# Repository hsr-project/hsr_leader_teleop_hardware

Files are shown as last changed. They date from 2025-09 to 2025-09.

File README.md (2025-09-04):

# THSR: Teleoperation Hardware for HSR

This repository publishes 3D data and documentation for a leader-side teleoperation hardware named THSR to be used with the Toyota Human Support Robot (HSR).

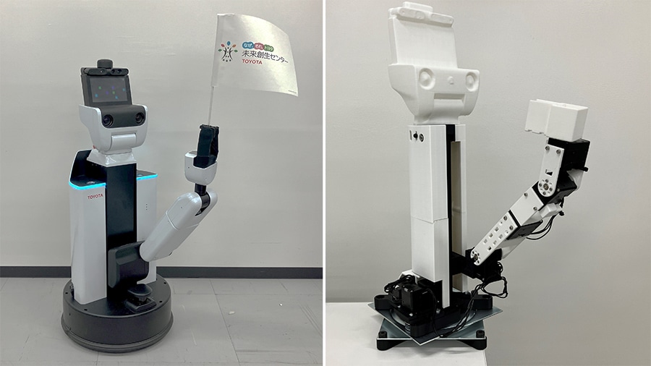
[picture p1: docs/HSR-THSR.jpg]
THSR


## Quick links

- Assembly model: [STEP/THSR-Total-000-A.STEP](STEP/THSR-Total-000-A.STEP)
- Printable parts (examples; see full sets under `STL/THSR-Arm`, `STL/THSR-Lift`, `STL/THSR-Turn`):
  - Arm: [STL/THSR-Arm/THSR-Arm-010.STL](STL/THSR-Arm/THSR-Arm-010.STL), etc.
  - Lift: [STL/THSR-Lift/THSR-Lift-010.STL](STL/THSR-Lift/THSR-Lift-010.STL), etc.
  - Turn: [STL/THSR-Turn/THSR-Turn-010.STL](STL/THSR-Turn/THSR-Turn-010.STL), etc.
- Assembly guide: [docs/THSR-組付手順書.pdf](docs/THSR-組付手順書.pdf)
- Bill of Materials (BOM): [docs/THSR-BOM.csv](docs/THSR-BOM.csv)

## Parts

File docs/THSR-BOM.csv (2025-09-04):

No | Unit | Item Name | Quantity | Remarks
1 | lift-assy | SSEBZ10-235 | 1 | misumi
2 | lift-assy | HTPA14S2M100-K-P3 | 2 | misumi
3 | lift-assy | CLBP3-5-3.5 | 4 | misumi
4 | lift-assy | SB693ZZ | 4 | misumi
5 | lift-assy | HFSB5-2020-264-TPW | 1 | misumi
6 | lift-assy | SSFR3-48-WFC0-J6-W12-V6-TB2 | 1 | misumi
7 | lift-assy | SSFR3-41-TA2-TB2 | 1 | misumi
8 | lift-assy | THSR-Lift-020 | 1 | 3D printed part, Black, PLA
9 | lift-assy | THSR-Lift-050-A | 2 | 3D printed part, Black, PLA
10 | lift-assy | HTBN500S2M-100 | 1 | misumi
11 | lift-assy | THSR-Lift-070 | 1 | 3D printed part, Black, PLA
12 | lift-assy | THSR-Lift-010-A | 1 | 3D printed part, Black, PLA, infill60%
13 | lift-assy | THSR-Lift-090 | 1 | 3D printed part, Black, PLA, infill60%
14 | lift-assy | THSR-Lift-080 | 1 | 3D printed part, Black, PLA
15 | lift-assy | CBE3-15 | 9 | misumi
16 | lift-assy | CBE5-15 | 1 | misumi
17 | lift-assy | CBE3-10 | 14 | misumi
18 | lift-assy | LBNR3 | 14 | misumi
19 | lift-assy | CBE3-6 | 4 | misumi
20 | lift-assy | CSHSM-SUS-M3-5 | 4 | misumi
21 | lift-assy | THSR-Lift-060 | 1 | 3D printed part, Black, PLA, infill60%
22 | lift-assy | SHNTP5-3 | 4 | misumi
23 | lift-assy | CBSH5-16 | 1 | misumi
24 | lift-assy | HTPA24S3M060-A-P6 | 1 | misumi
25 | lift-assy | GEABB0.5-15-8-K-3 | 1 | misumi
26 | pulley-assy | XM430-W210-T | 1 | ROBOTIS
27 | pulley-assy | HILS-turn-shaft-1107 | 1 | Custom part Meviy, MVTUP-APN-3ZM-M1JEH (Meviy part number)
28 | pulley-assy | THSR-Lift-040-A | 1 | 3D printed part, Black, PLA
29 | pulley-assy | SB676ZZ | 2 | misumi
30 | pulley-assy | CBSST2-4 | 4 | misumi
31 | gear-assy | XC-330-T181-T | 1 | ROBOTIS
32 | gear-assy | GEABB0.5-50-2-B-4 | 1 | misumi
33 | gear-assy | HILS-lift-shaft-holder-1113 | 1 | Custom part Meviy, MVTUP-APN-3ZN-NNWBE (Meviy part number)
34 | gear-assy | THSR-Lift-030-A | 1 | 3D printed part, Black, PLA
35 | gear-assy | SB674ZZ | 1 | misumi
36 | gear-assy | SCB2-12 | 3 | misumi
37 | gear-assy | SCB2-6 | 4 | misumi
38 | lift-assy | SCB2.5-8 | 4 | misumi
39 | lift-assy | CR-4 | 1 | misumi
40 | lift-assy | SCB4-20 | 1 | misumi
41 | arm-assy | THSR-Arm-010-A | 1 | 3D printed part, Black, PLA, infill60%
42 | arm-assy | XM430-W350-T | 4 | ROBOTIS
43 | arm-assy | HN12-I101 Set | 2 | ROBOTIS
44 | arm-assy | THSR-Arm-030 | 1 | 3D printed part, White, PLA
45 | arm-assy | THSR-Arm-040 | 1 | 3D printed part, White, PLA
46 | arm-assy | THSR-Arm-050 | 1 | 3D printed part, White, PLA
47 | arm-assy | THSR-Arm-020 | 1 | 3D printed part, White, PLA
48 | arm-assy | THSR-Arm-060-A | 1 | 3D printed part, White, PLA
49 | arm-assy | THSR-Arm-070 | 1 | 3D printed part, White, PLA
50 | arm-assy | THSR-Arm-080 | 1 | 3D printed part, White, PLA
51 | arm-assy | SCB2.5-5 | 14 | misumi
52 | arm-assy | SCB2-4 | 23 | misumi
53 | arm-assy | SCB2.5-15 | 4 | misumi
54 | turn-assy | THS-70160 | 1 | misumi
55 | turn-assy | HTPA60S3M060-A-P30 | 1 | misumi
56 | turn-assy | 60S3M270G | 1 | misumi
57 | turn-assy | THSR-Turn-010-A | 1 | 3D printed part, Black, PLA
58 | turn-assy | CBSH8-16 | 8 | misumi
59 | turn-assy | KNTR8 | 8 | misumi
60 | turn-assy | THSR-Turn-020-A | 1 | 3D printed part, Black, PLA
61 | turn-assy | CBE5-20 | 4 | misumi
62 | Cover | THSR-Lift-100-A | 1 | 3D printed part, White, PLA
63 | Cover | THSR-Lift-110-A | 1 | 3D printed part, White, PLA
64 | Cover | CBE3-8 | 6 | misumi
65 | other | U2D2 | 1 | ROBOTIS
66 | other | U2D2 PHB Set | 1 | ROBOTIS
67 | other | aka-12070 | 1 | ROBOTIS
68 | other | Robot Cable-X3P 240mm 10pcs | 1 | ROBOTIS, Pack of 10, 2 used per unit
69 | other | Nintendo Switch Joy-Con (L/R) | 1 | -
70 | other | Nintendo Switch Joy-Con charging grip | 1 | -
71 | lift-assy | SPWF5 | 1 | misumi
72 | lift-assy | SMKB5-5 | 1 | misumi
73 | lift-assy | WSSS8-6-2.5 | 1 | misumi
74 | lift-assy | PACK-MSSU4-4-YBM | 1 | misumi, Pack of 10, used for turn small pulley, 1 used per unit
75 | lift-assy | PACK-MSSU3-3-YBM | 1 | misumi, Pack of 10, used for lift gear/pulley, 3 used per unit
76 | turn-assy | PACK-MSSU5-6-YBM | 1 | misumi, Pack of 10, used for turn large pulley, 2 used per unit

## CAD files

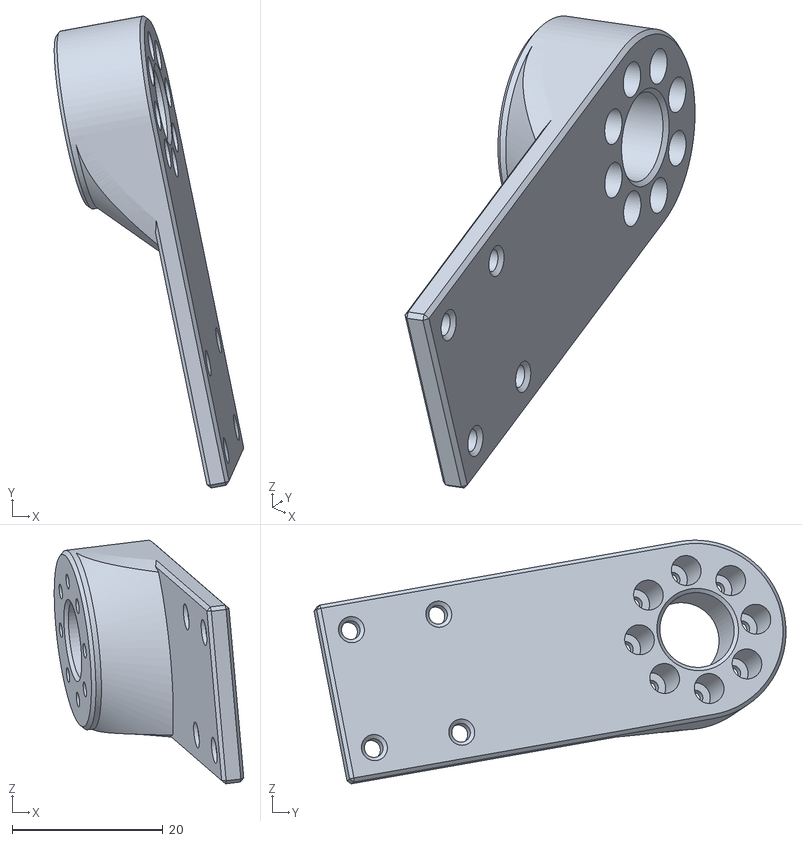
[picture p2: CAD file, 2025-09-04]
STL/THSR-Arm/THSR-Arm-050.STL
25.2 x 62.6 x 32.3

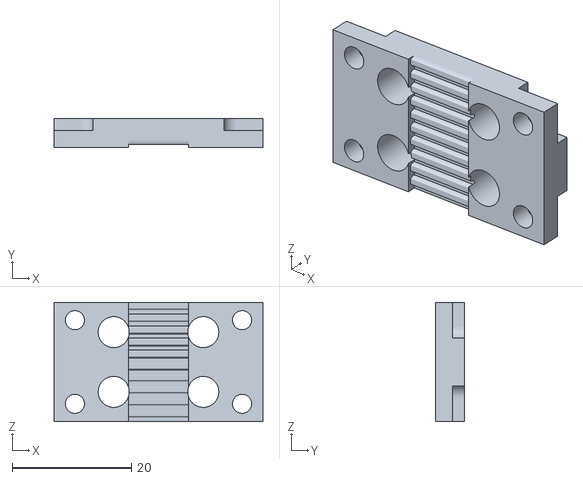
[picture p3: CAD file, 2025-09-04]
STL/THSR-Lift/THSR-Lift-070.STL
35.0 x 4.86 x 20.0

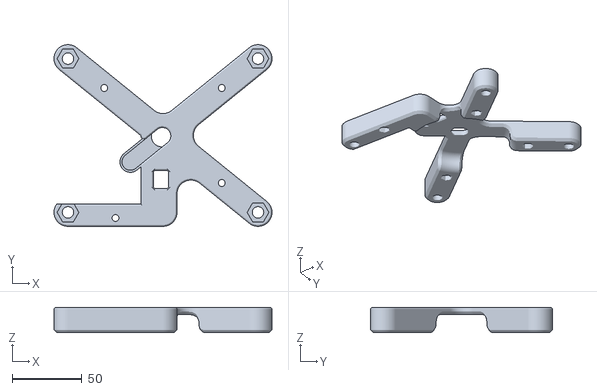
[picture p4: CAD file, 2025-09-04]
STL/THSR-Turn/THSR-Turn-020.stl
156.0 x 130.0 x 18.0

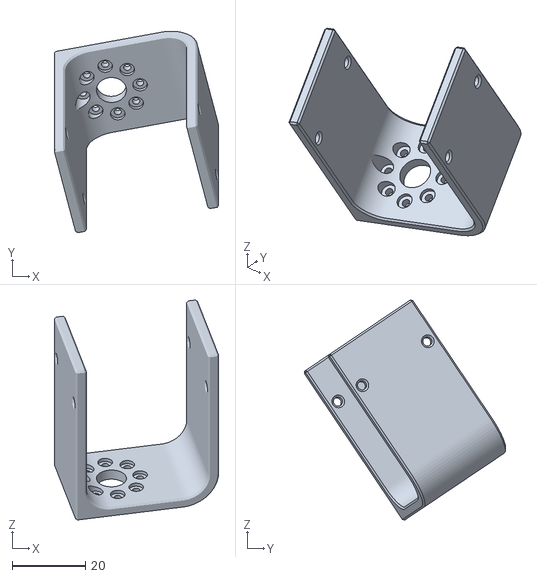
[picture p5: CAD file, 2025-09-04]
STL/THSR-Arm/THSR-Arm-030.STL
44.9 x 55.0 x 60.0

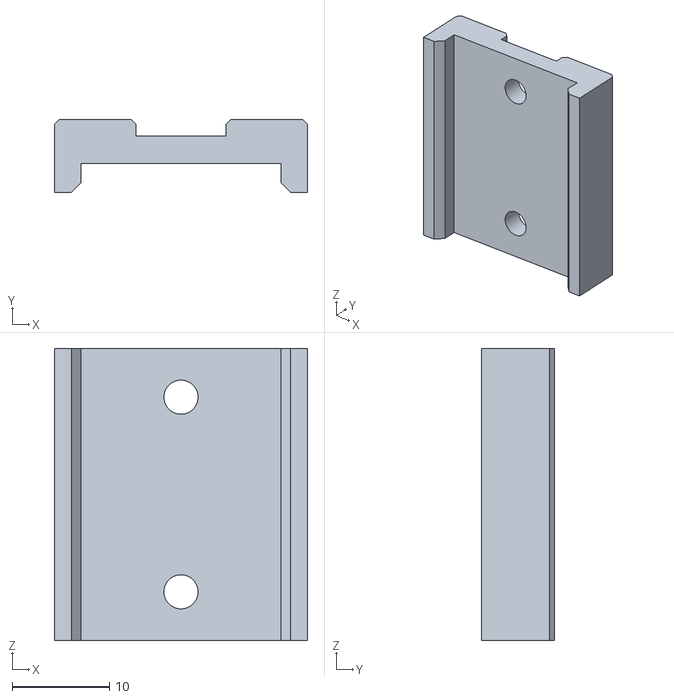
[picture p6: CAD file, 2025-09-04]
STL/THSR-Lift/THSR-Lift-050.stl
26.0 x 7.50 x 30.0

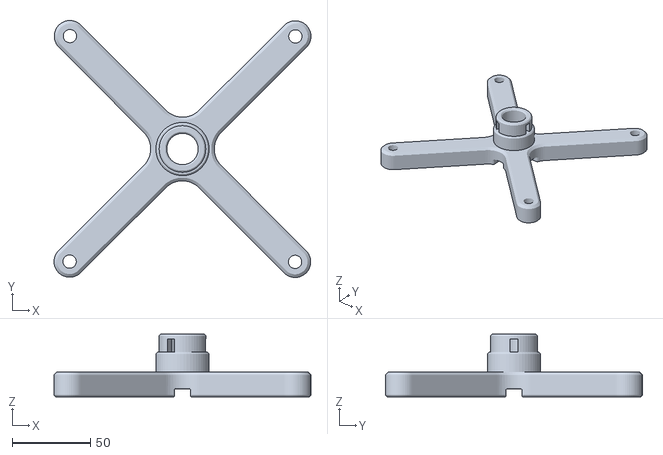
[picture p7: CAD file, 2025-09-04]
STL/THSR-Turn/THSR-Turn-010.STL
164.2 x 164.2 x 40.0

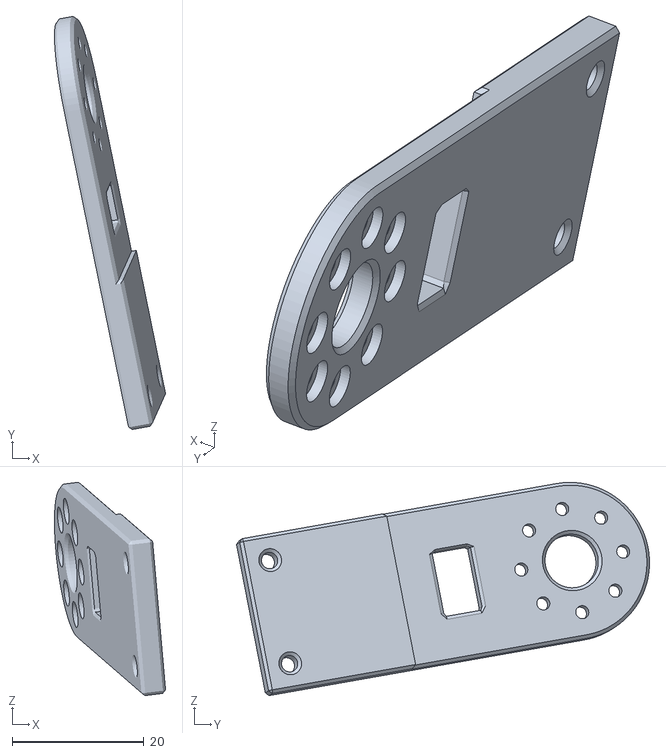
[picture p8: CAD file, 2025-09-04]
STL/THSR-Arm/THSR-Arm-040.STL
16.8 x 62.6 x 32.3

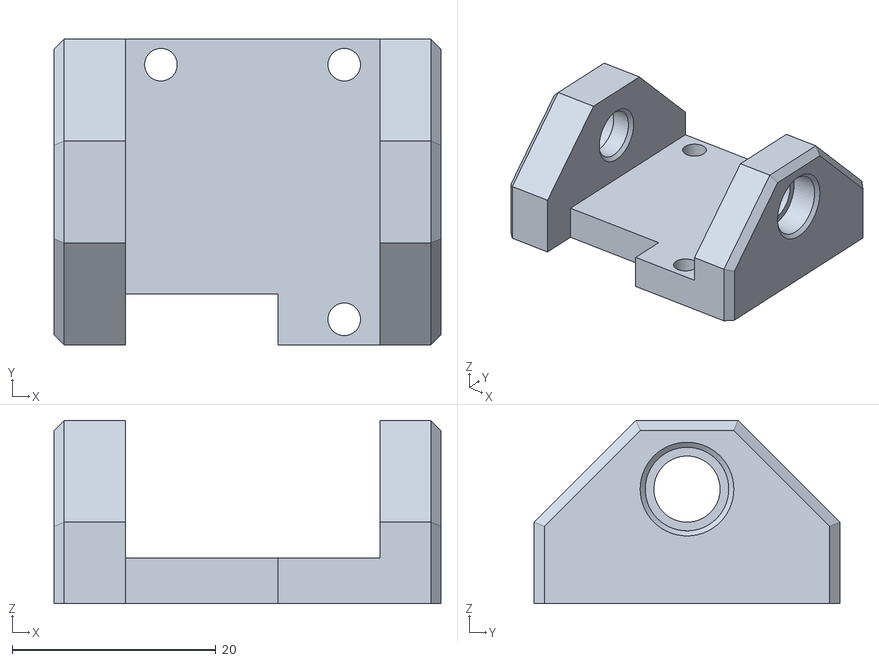
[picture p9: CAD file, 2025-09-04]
STL/THSR-Lift/THSR-Lift-020.STL
38.0 x 30.0 x 18.0

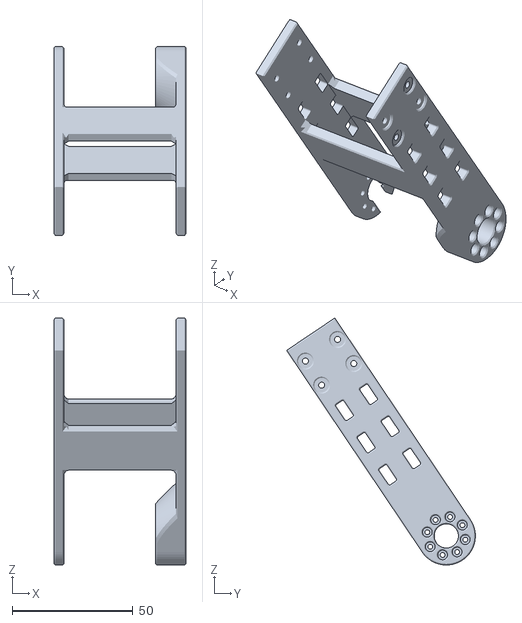
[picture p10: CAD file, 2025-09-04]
STL/THSR-Arm/THSR-Arm-020.STL
54.5 x 78.0 x 102.1

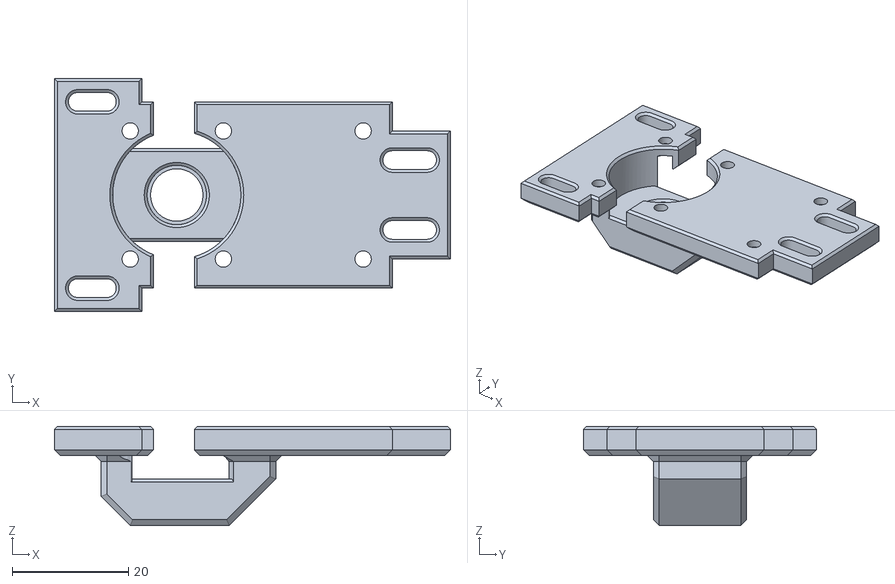
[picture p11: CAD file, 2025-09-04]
STL/THSR-Lift/THSR-Lift-040.STL
68.0 x 40.0 x 17.0

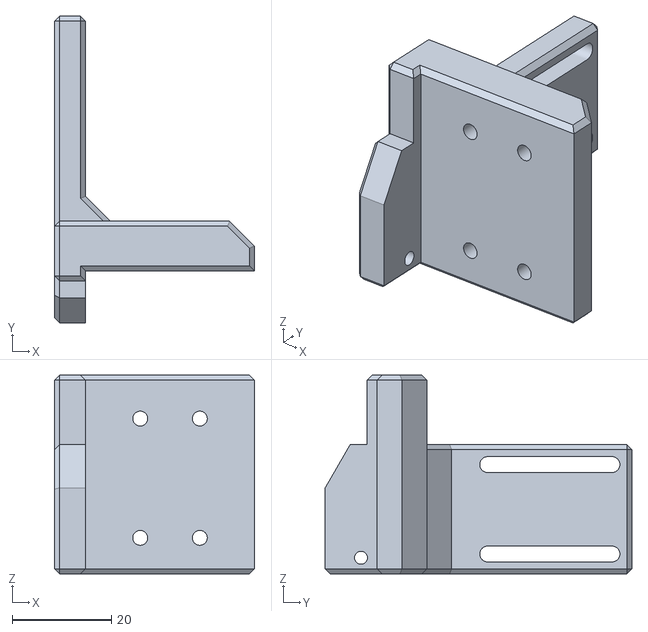
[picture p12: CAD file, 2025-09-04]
STL/THSR-Arm/THSR-Arm-010.STL
40.2 x 61.7 x 40.0

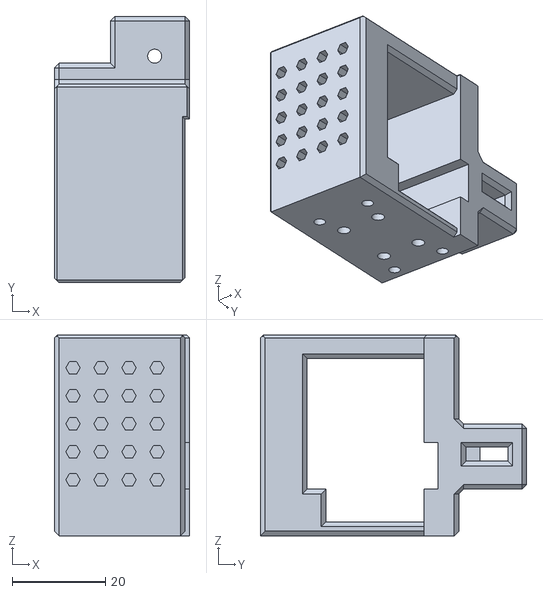
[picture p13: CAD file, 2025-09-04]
STL/THSR-Lift/THSR-Lift-060.stl
29.0 x 57.0 x 43.0

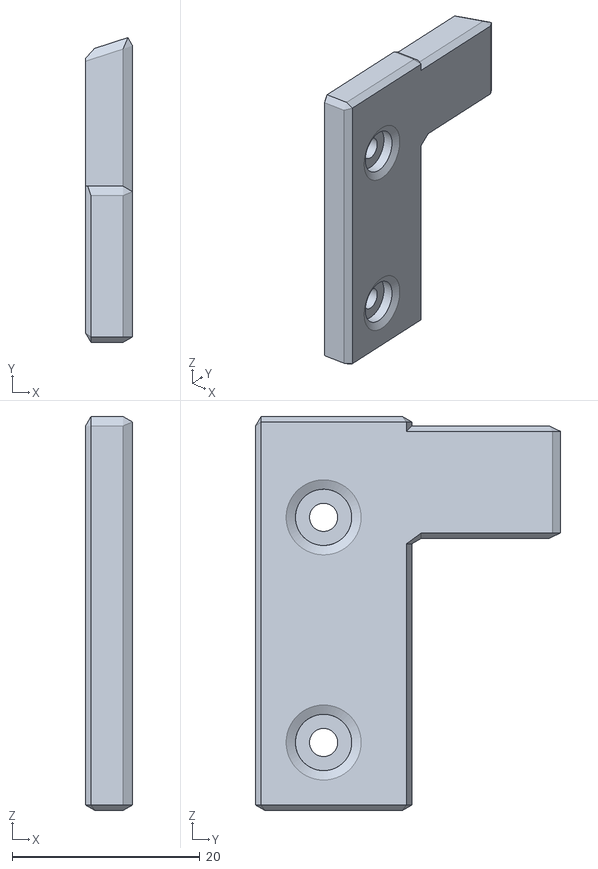
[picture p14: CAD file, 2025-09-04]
STL/THSR-Arm/THSR-Arm-070.STL
5.00 x 32.5 x 42.0

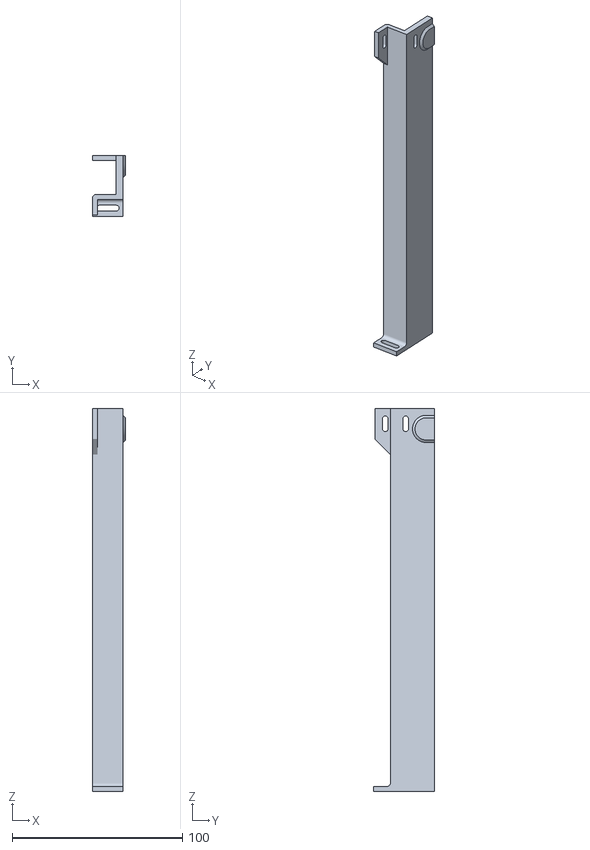
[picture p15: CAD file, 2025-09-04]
STL/THSR-Lift/THSR-Lift-100.stl
19.5 x 36.0 x 225.0

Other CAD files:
STL/THSR-Arm/THSR-Arm-080.STL
STL/THSR-Lift/THSR-Lift-080.STL
STL/THSR-Arm/THSR-Arm-060.STL
STL/THSR-Lift/THSR-Lift-110.stl
STL/THSR-Lift/THSR-Lift-010.STL
STL/THSR-Lift/THSR-Lift-030.STL
STL/THSR-Lift/THSR-Lift-090.STL
